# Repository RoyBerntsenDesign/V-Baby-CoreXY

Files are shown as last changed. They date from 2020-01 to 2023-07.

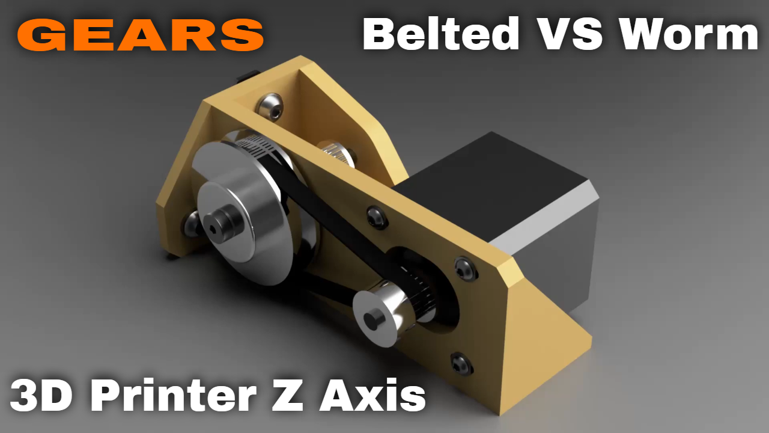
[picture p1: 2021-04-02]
Part Print Files/Stock Parts/Base Frame Parts/Z Gear Belted/Belted Gear 00.png

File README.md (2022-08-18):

# V-Baby CoreXY 3d Printer
The desktop CoreXY 3d Printer by Roy Berntsen - OpenSource - OpenBuilds Machine

In this repository you will find the print files, source files and documentation for the V-Baby 3D printer. If you are missing a part or information of feel free to file an issue on github

You can be a supporter of the develompent on patreon here: https://www.patreon.com/pro3d?fan_landing=true
Or if you want to buy me a coffe to keep the pace going in this project:

<a href="https://www.buymeacoffee.com/pro3d" target="_blank">Buy Me A Coffee</a>

Community links: https://www.facebook.com/vking3d/ - https://www.facebook.com/groups/viking3d/

All files are released according to the following license unless specified differently in the file or directory:
CC-by-NC: http://creativecommons.org/licenses/by-nc/3.0/

Roy Berntsen - Research and Development

3d model for view and download
V1 Top Assembly: https://a360.co/3PA3aYa

V-Baby 12 00

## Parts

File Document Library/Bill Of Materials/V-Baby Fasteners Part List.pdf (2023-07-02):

Part Name | Description | Quantity | Order Quantity
M2 NUT | Nut Standard | 2 | 2
M2,5 Nut | Nut Standard | 4 | 4
M2,5x16 BH | Low Profile Head | 4 | 4
M2x10 BH | Low Profile Head | 2 | 2
M3 Lock Nut | Nut Nylon Lock | 2 | 2
M3 Nut | Nut Standard | 11 | 11
M3 WASHER | Washer Standard | 15 | 15
M3x06 BH | Low Profile Head | 6 | 6
M3x08 BH | Low Profile Head | 9 | 9
M3x10 BH | Low Profile Head | 5 | 5
M3x12 BH | Low Profile Head | 8 | 8
M3x30 HEX | Hex Bolt | 2 | 2
M4 LOCK NUT | NUT Nylon LOCK | 5 | 5
M4 NUT | Nut Standard | 5 | 5
M4 WASHER | Washer Standard | 13 | 13
M4x10 BH | Low Profile Head | 6 | 6
M4x12 BH | Low Profile Head | 2 | 2
M4x16 BH | Low Profile Head | 1 | 1
M4x16 HEX | Hex Bolt | 3 | 3
M4x20 HEX | Hex Bolt | 1 | 1
M4x30 BH | Low Profile Head | 1 | 1
M5 LOCK NUT | NUT Nylon LOCK | 28 | 30
M5 Nut | Nut Standard | 6 | 6
M5 Nut Drop-In | Nut Drop In | 50 | 50
M5 Precision Shim 5X6X1 Precision Shim | 63 | 70
M5 T-Nut OB | OpenBuilds Tee Nut | 143 | 150
M5 WASHER | Washer Standard | 200 | 200
M5x10 BH | Low Profile Head | 142 | 150
M5x12 BH | Low Profile Head | 8 | 8
M5x16 BH | Low Profile Head | 1 | 1
M5x20 BH | Low Profile Head | 2 | 2
M5x25 BH | Low Profile Head | 2 | 2
M5x30 BH | Low Profile Head | 18 | 18
M5x35 BH | Low Profile Head | 8 | 8
M5x35 Bearing pin 5mm Bearing pin | 4 | 1x10
Number of fasteners | | 782 | 802
Approx Price/Pcs | | | $0.10
Approx Fasteners Price | $80.20

Part Name | Description

NB! See Component List

Quantity

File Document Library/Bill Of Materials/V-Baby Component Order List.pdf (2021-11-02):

V-Baby CoreXY Part (https://www.buymeacoffee.com/pro3d) List

MakerSupplies Mechanical Kit (https://makersupplies.dk/en/corexy-3d-printer/446-corexy-3d-printer-small-mechanical-kit-for-v-baby-corexy-3d-printer-200mm.html) <<-- ALL HARDWARE KIT HERE $334.00
Part Name | Description | Quantity | AliExpress Link | Price | Optional Component Price2
10mm Belt Idler Smooth | Smooth Idler for 10mm belt | 4 | Size: W 11mm without t (https://s.click.aliexpress.com/e/_AVt9fH) | $16.00
10mm Belt Idler Thoothed | Thoothed Idler for 10mm belt | 2 | Size: W 11mm with t (https://s.click.aliexpress.com/e/_AVt9fH) | $10.00
10mm Belt Z Gear Pulley | Pulley for the Belted Z Gear | 1 | Size: For 10mm 1 pcs (https://s.click.aliexpress.com/e/_Ae26J6) | $5.00
10mm Timing Belt | 2GT Timing Belt 10W 2 Meter | 4 meter | Size: 2M Color: 2GT 10MM (https://s.click.aliexpress.com/e/_A1bwlD) | $22.00
6mm Belt Idler Smooth | Smooth Idler for 6mm belt | 2 | Size: W 7mm without t (https://s.click.aliexpress.com/e/_AVt9fH) | $10.00
6mm Belt Idler Thoothed | Thoothed Idler for 6mm belt | 6 | Size: W 7mm with t (https://s.click.aliexpress.com/e/_AVt9fH) | $28.00
6mm Belt Motor Pulley | GT2 20T 6W 5mm Bore | 2 | Size: Bore 5 width 6 (https://s.click.aliexpress.com/e/_Aag7aB) | $11.00
6mm Timing Belt | 2GT Timing Belt 6W 4 Meter | 4 meter | Size: 4M-6MM-2GT (https://s.click.aliexpress.com/e/_A3kbnW) | $19.00
Belt Idler Bearing shafts | Bearing shafts 5mm | 1x6 | 5mm Length: 35mm 6PC (https://s.click.aliexpress.com/e/_A2xCLl) | $3.00
Belt Idler Precision Shim | 6.5x5x1 mm Precision Shim | 80 | Size: 6.5x5x1mm (https://www.aliexpress.com/item/32874190317.html) | $15.00
Bowden Tube | 1.9ID 4OD Filament Tube | 1 | Size: Black 1M (https://s.click.aliexpress.com/e/_A8XHCT) | $2.50
Cable Loom Tube | Tube for Hotend Cables | 1 | 20mmx1m Cable Loom (https://s.click.aliexpress.com/e/_dTFkJul) | $2.50
Cable Sleeve Nylon | Sleeve for Heatbed cables | 1 | 10 mm Sleeve (https://s.click.aliexpress.com/e/_dSOVNYp) | $8.00
Controller Board | Duet WIFI Clone w/TMC2660 | 1 | BTT DUET WIFI Clone (https://s.click.aliexpress.com/e/_AK6uHu) | $60.00
Extruder | BMG Type Filament Extruder | 1 | TriangleLab BMG (https://s.click.aliexpress.com/e/_AoiXQz) | $31.00
Fan for Cabinet cooling | 4010 Axial Fan 12/24V | 2 | Blade Color: 24V Ball (https://s.click.aliexpress.com/e/_9AUPbv) | $10.00
Fan for Hotend cooling | 4010 Blower Fan 12/24V | 1 | Blade Color: 24V Ball 9500RPM (https://s.click.aliexpress.com/e/_ATvGsB) | $2.00
Fan For Part Cooling | 3010 Blower Fan 5/12 24V | 2 | Blade Color: 24v dual ball (http://s.click.aliexpress.com/e/bele3ZZI) | $10.00
Heatbed Build Plate | Milled Cast Aluminum | 1 | 6mm 210x210 mm (https://makersupplies.dk/metal/816-metal-cnc-milled-cast-aluminum-plate.html) | $30.00 | Rolled Aluminum 5mm (http://s.click.aliexpress.com/e/bYQLqeBW) | $16.00
Hotend | Dragon Hotend | 1 | Dragonfly Phateus Color: BMO (https://s.click.aliexpress.com/e/_9z8pWX) | $73.00
Nema 17 1.8 A | Stepper motor 1.8 Amp | 1x5 | 5Pack & Cable (https://s.click.aliexpress.com/e/_AtomW3) | $30.00
Optical Endstops | XY(Z) Endstops | 1x6 | 6Pack Endstops (http://s.click.aliexpress.com/e/Im2VNR3) | $4.00
Power Switch | 10A 250VAC Fused Switch | 1 | 10A Fused Switch (http://s.click.aliexpress.com/e/blNcy7Lw) | $8.50
Powersupply | 24V 240W PSU | 1 | 24V 10A 240W (http://s.click.aliexpress.com/e/4GAsFeg) | $20.00
Safety Fuse | Thermal Safety Fuse for SSR | 1 | 135 Deg Fuse (http://s.click.aliexpress.com/e/bu7dz62U) | $2.00
Silicon Bed Heater | 200x200 110V/220V Heater | 1 | Kenoovo 240V 400W (https://s.click.aliexpress.com/e/_APr1gj) | $40.00
Solid State Relay | Silicone Heater Relay Switch | 1 | SSR 40DA (http://s.click.aliexpress.com/e/ckUQTj4c) | $3.50
Z 3:1 GT2 Gear | GT2 Pulleys and 200 mm Belt | 1 | Size: 20T5 - 60T5:Color: 200MM (https://s.click.aliexpress.com/e/_9QiZzH) | $8.50
Z Drive Gear Bearings | 625RS Bearings | 1x10 | 10Pcs 625RS (https://s.click.aliexpress.com/e/_9AmX7Z) | $19.00
Z Drive Gear Pulley Bolt | Bolt for the Gear Pulleys | 1 | Dia 5mm Length: 60mm (https://s.click.aliexpress.com/e/_A6tRQF) | $6.00
Z Leveling Probe | 3D Touch Leveling Probe | 1 | 3D Touch (http://s.click.aliexpress.com/e/bhxMAOUo) | $14.00
Component Total Price | | | | $523.50
Price inclusive mech kit | | | | USD 857.50

Research, Development & Design by:
Roy Berntsen M.Sc. Engineering Designer (https://www.buymeacoffee.com/pro3d)

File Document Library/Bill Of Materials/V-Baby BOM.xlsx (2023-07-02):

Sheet: OpenBuild Part List
Exstrusions | Part Name | Description | Quantity | Length mm | OpenBuilds Kit | AliExpress Parts |  | Price
 |  |  |  |  | Frame - Wheels - Brackets - Fasterners + Cutts & Tapping (https://makersupplies.dk/corexy-3d-printer/446-corexy-3d-printer-beta-version-base-mechanical-kit-for-baby-corexy-3d-printer.html)
X Direction | 2020 V-Slot X Axis | 310mm V-Slot | 4 | 1240
Y Direction | 2020 V-Slot Y Axis | 350mm V-Slot Tapped | 4 | 1400
Z Direction | 2020 V-Slot Z Axis | 340mm V-Slot | 5 | 1700
X Axis | 2020 V-Slot X Axis | 295mm V-Slot | 1 | 295
X Bed Frame | 2020 V-Slot Bed Frame X | 2020 V-Slot 290 | 1 | 290
Y Bed Frame | 2020 V-Slot Bed Frame Y | 2020 V-Slot 350 | 2 | 700 |  | No cuts - No tapps
Total | V-Slot | V-Slot in Meter |  | 5625 |  | 17x350 (https://s.click.aliexpress.com/e/_AVYFX8) | V-Slots | $21.00
 |  |  |  |  |  | Shipping |  | $108.00
Printer | V-Wheel Mini Assy | V-Wheel Mini Assy | 18 |  |  | 2 X 10 Pack (http://s.click.aliexpress.com/e/bnir7Lze) | Wheels | $15.00
Base Frame | 2820 L Bracket | Corner Bracket | 30 |  |  | 2 X 20 Pack (http://s.click.aliexpress.com/e/biEt0RTE) | Brackets | $14.00
OpenBuild Part Price |  |  |  |  | $360.00 |  |  | $158.00
OpenBuild Parts Price |  |  |  |  | $360.00 | AliExpress |  | $158.00
Component Part Price |  |  |  |  | $523.50 | Component Part Price |  | $523.50
Cable Management |  |  |  |  | - | Cable Management |  | -
Fasteners Part Price |  |  |  |  | Included | Fasteners Part Price |  | $80.20
Total Printer Price wo/Tax & Shipping |  |  |  |  | $883.50 | Total |  | $761.70

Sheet: V-Slot Calculator
V-Slot Calculator
V-Baby 200 |  | Pcs | V-Baby 250 |  | V-Baby 300
X Base Frame | 310 | x4 | 360 |  | 410
Y Base Frame | 350 | x4 | 400 | Tapped | 450 | Tapped
Z Base Frame | 340 | x5 | 390 |  | 440
X Bed Frame | 290 | x1 | 340 |  | 390
Y Bed Frame | 350 | x2 | 400 |  | 450
X Axis | 295 | x1 | 345 |  | 395
V-Baby XYZ
Configure Your Own
Add your wanted travel here: |  | mm | Needed Extrusion Length: |  | Pcs
X Base Frame | 390 | X | 500 |  | x4
Y Base Frame | 350 | Y | 500 |  | x4 | Tapped
Z Base Frame | 360 | Z | 500 |  | x5
X Bed Frame |  |  | 480 |  | x1
Y Bed Frame |  |  | 500 |  | x2
X Axis |  |  | 485 |  | x1
You Can Support the Development Here:
https://www.buymeacoffee.com/pro3d
https://www.patreon.com/pro3d

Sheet: Component Part List
 |  |  | V-Baby CoreXY Part List
MakerSupplies Mechanical Kit (https://makersupplies.dk/en/corexy-3d-printer/446-corexy-3d-printer-small-mechanical-kit-for-v-baby-corexy-3d-printer-200mm.html) |  | <<-- ALL HARDWARE KIT HERE |  | $334.00
Part Name | Description | Quantity | AliExpress Link | Price | Optional Component | Price2
10mm Belt Idler Smooth | Smooth Idler for 10mm belt | 4 | Size: W 11mm without t (https://s.click.aliexpress.com/e/_AVt9fH) | $16.00
10mm Belt Idler Thoothed | Thoothed Idler for 10mm belt | 2 | Size: W 11mm with t (https://s.click.aliexpress.com/e/_AVt9fH) | $10.00
10mm Belt Z Gear Pulley | Pulley for the Belted Z Gear | 1 | Size: For 10mm 1 pcs (https://s.click.aliexpress.com/e/_Ae26J6) | $5.00
10mm Timing Belt | 2GT Timing Belt 10W 2 Meter | 4 meter | Size: 2M Color: 2GT 10MM (https://s.click.aliexpress.com/e/_A1bwlD) | $22.00
6mm Belt Idler Smooth | Smooth Idler for 6mm belt | 2 | Size: W 7mm without t (https://s.click.aliexpress.com/e/_AVt9fH) | $10.00
6mm Belt Idler Thoothed | Thoothed Idler for 6mm belt | 6 | Size: W 7mm with t (https://s.click.aliexpress.com/e/_AVt9fH) | $28.00
6mm Belt Motor Pulley | GT2 20T 6W 5mm Bore | 2 | Size: Bore 5 width 6 (https://s.click.aliexpress.com/e/_Aag7aB) | $11.00
6mm Timing Belt | 2GT Timing Belt 6W 4 Meter | 4 meter | Size: 4M-6MM-2GT (https://s.click.aliexpress.com/e/_A3kbnW) | $19.00
Belt Idler Bearing shafts | Bearing shafts 5mm | 1x6 | 5mm Length: 35mm 6PC (https://s.click.aliexpress.com/e/_A2xCLl) | $3.00
Belt Idler Precision Shim | 6.5x5x1 mm Precision Shim | 80 | Size: 6.5x5x1mm (https://www.aliexpress.com/item/32874190317.html) | $15.00
Bowden Tube | 1.9ID 4OD Filament Tube | 1 | Size: Black 1M (https://s.click.aliexpress.com/e/_A8XHCT) | $2.50
Cable Loom Tube | Tube for Hotend Cables | 1 | 20mmx1m Cable Loom (https://s.click.aliexpress.com/e/_dTFkJul) | $2.50
Cable Sleeve Nylon | Sleeve for Heatbed cables | 1 | 10 mm Sleeve (https://s.click.aliexpress.com/e/_dSOVNYp) | $8.00
Controller Board | Duet WIFI Clone w/TMC2660 | 1 | BTT DUET WIFI Clone (https://s.click.aliexpress.com/e/_AK6uHu) | $60.00
Extruder | BMG Type Filament Extruder | 1 | TriangleLab BMG (https://s.click.aliexpress.com/e/_AoiXQz) | $31.00
Fan for Cabinet cooling | 4010 Axial Fan 12/24V | 2 | Blade Color: 24V Ball (https://s.click.aliexpress.com/e/_9AUPbv) | $10.00
Fan for Hotend cooling | 4010 Blower Fan 12/24V | 1 | Blade Color: 24V Ball 9500RPM (https://s.click.aliexpress.com/e/_ATvGsB) | $2.00
Fan For Part Cooling | 3010 Blower Fan 5/12 24V | 2 | Blade Color: 24v dual ball (http://s.click.aliexpress.com/e/bele3ZZI) | $10.00
Heatbed Build Plate | Milled Cast Aluminum | 1 | 6mm 210x210 mm (https://makersupplies.dk/metal/816-metal-cnc-milled-cast-aluminum-plate.html) | $30.00 | Rolled Aluminum 5mm (http://s.click.aliexpress.com/e/bYQLqeBW) | $16.00
Hotend | Dragon Hotend | 1 | Dragonfly Phateus Color: BMO (https://s.click.aliexpress.com/e/_9z8pWX) | $73.00
Nema 17 1.8 A | Stepper motor 1.8 Amp | 1x5 | 5Pack & Cable (https://s.click.aliexpress.com/e/_AtomW3) | $30.00
Optical Endstops | XY(Z) Endstops | 3 | 3PCS (https://s.click.aliexpress.com/e/_ASe8tS) | $4.00
Power Switch | 10A 250VAC Fused Switch | 1 | 10A Fused Switch (https://s.click.aliexpress.com/e/_AX4lXw) | $8.50
Powersupply | 24V 240W PSU | 1 | 24V 10A 240W (http://s.click.aliexpress.com/e/4GAsFeg) | $20.00
Safety Fuse | Thermal Safety Fuse for SSR | 1 | 135 Deg Fuse (http://s.click.aliexpress.com/e/bu7dz62U) | $2.00
Silicon Bed Heater | 200x200 110V/220V Heater | 1 | Kenoovo 240V 400W (https://s.click.aliexpress.com/e/_APr1gj) | $40.00
Solid State Relay | Silicone Heater Relay Switch | 1 | SSR 40DA (http://s.click.aliexpress.com/e/ckUQTj4c) | $3.50
Z 3:1 GT2 Gear | GT2 Pulleys and 200 mm Belt | 1 | Size: 20T5 - 60T5:Color: 200MM (https://s.click.aliexpress.com/e/_9QiZzH) | $8.50
Z Drive Gear Bearings | 625RS Bearings | 1x10 | 10Pcs 625RS (https://s.click.aliexpress.com/e/_9AmX7Z) | $19.00
Z Drive Gear Pulley Bolt | Bolt for the Gear Pulleys | 1 | Dia 5mm Length: 60mm (https://s.click.aliexpress.com/e/_A6tRQF) | $6.00
Z Leveling Probe | 3D Touch Leveling Probe | 1 | 3D Touch (http://s.click.aliexpress.com/e/bhxMAOUo) | $14.00
Component Total Price |  |  |  | $523.50
Price inclusive mech kit |  |  |  | USD 857.50

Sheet: Fasteners
Part Name | Description | Quantity | Order Quantity |  | Part Name | Description | Quantity
M2 NUT | Nut Standard | 2 | 2
M2,5 Nut | Nut Standard | 4 | 4
M2,5x16 BH | Low Profile Head | 4 | 4
M2x10 BH | Low Profile Head | 2 | 2
M3 Lock Nut | Nut Nylon Lock | 2 | 2
M3 Nut | Nut Standard | 11 | 11
M3 WASHER | Washer Standard | 15 | 15
M3x06 BH | Low Profile Head | 6 | 6
M3x08 BH | Low Profile Head | 9 | 9
M3x10 BH | Low Profile Head | 5 | 5
M3x12 BH | Low Profile Head | 8 | 8
M3x30 HEX | Hex Bolt | 2 | 2
M4 LOCK NUT | NUT Nylon LOCK | 5 | 5
M4 NUT | Nut Standard | 5 | 5
M4 WASHER | Washer Standard | 13 | 13
M4x10 BH | Low Profile Head | 6 | 6
M4x12 BH | Low Profile Head | 2 | 2
M4x16 BH | Low Profile Head | 1 | 1
M4x16 HEX | Hex Bolt | 3 | 3
M4x20 HEX | Hex Bolt | 1 | 1
M4x30 BH | Low Profile Head | 1 | 1
M5 LOCK NUT | NUT Nylon LOCK | 28 | 30
M5 Nut | Nut Standard | 6 | 6
M5 Nut Drop-In | Nut Drop In | 50 | 50
M5 Precision Shim | 5X6X1 Precision Shim | 63 | 70 | NB! See Component List
M5 T-Nut OB | OpenBuilds Tee Nut | 143 | 150
M5 WASHER | Washer Standard | 200 | 200
M5x10 BH | Low Profile Head | 142 | 150
M5x12 BH | Low Profile Head | 8 | 8
M5x16 BH | Low Profile Head | 1 | 1
M5x20 BH | Low Profile Head | 2 | 2
M5x25 BH | Low Profile Head | 2 | 2
M5x30 BH | Low Profile Head | 18 | 18
M5x35 BH | Low Profile Head | 8 | 8
M5x35 Bearing pin | 5mm Bearing pin (https://s.click.aliexpress.com/e/_DDzLeEd) | 4 | 1x10
Number of fasteners |  | 782 | 802
Approx Price/Pcs |  |  | $0.10
Approx Fasteners Price |  |  | $80.20

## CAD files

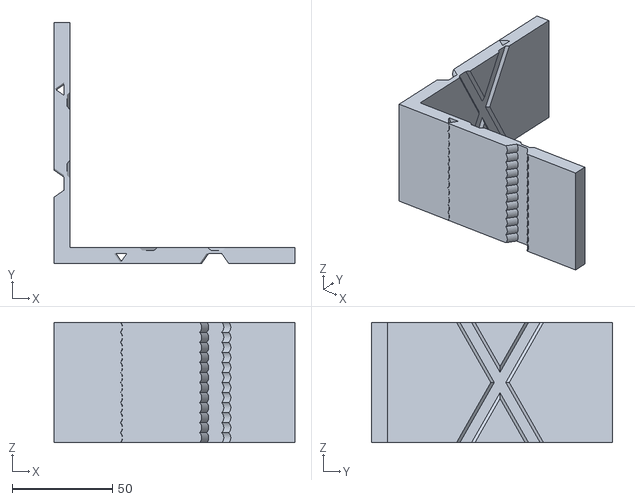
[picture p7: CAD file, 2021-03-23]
Part Print Files/Calibration Files/ringing_tower.stl
120.0 x 120.0 x 60.0

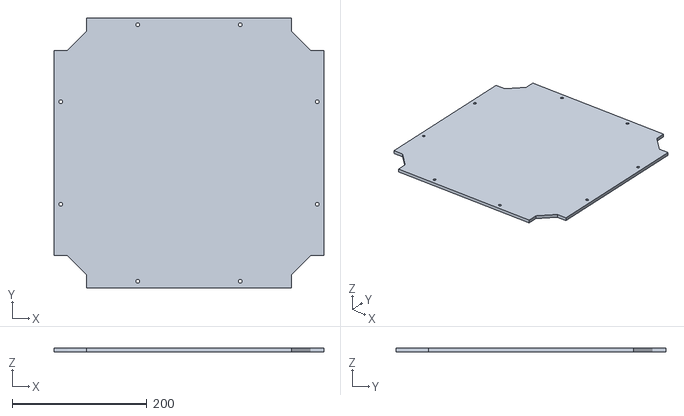
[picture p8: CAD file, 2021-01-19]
Part Print Files/Option Parts/250 Panels/250 Bottom Plate_1x.stl
400.0 x 400.0 x 6.00

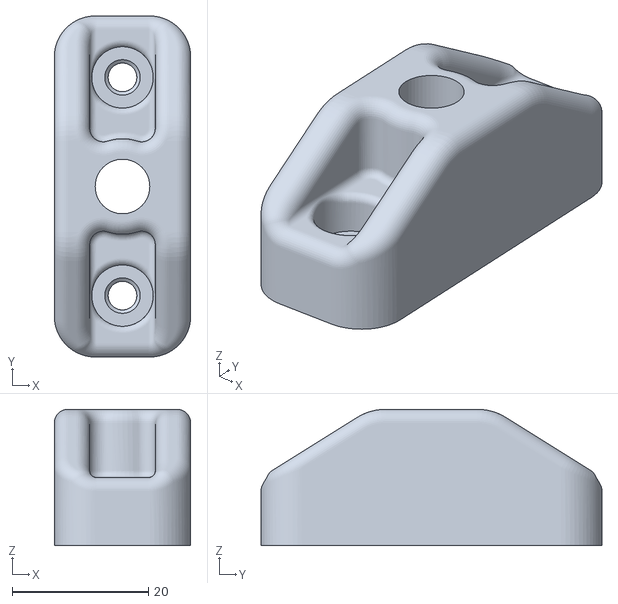
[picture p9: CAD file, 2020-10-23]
Part Print Files/Option Parts/Bearing Spool Holder/Spool Holder Base 1x_SN_BN_100%.stl
20.0 x 50.0 x 20.0

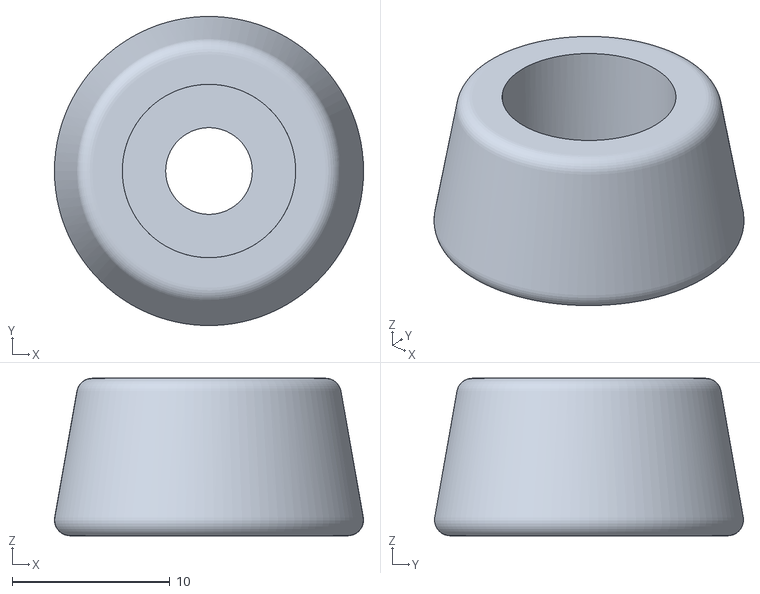
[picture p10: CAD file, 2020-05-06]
Part Print Files/Option Parts/Leg Parts/Leg TPU Bumper.stl
19.6 x 19.6 x 10.00

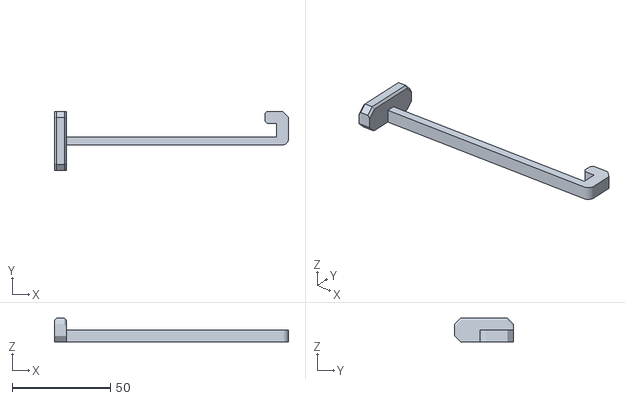
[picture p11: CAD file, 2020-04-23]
Part Print Files/Option Parts/Tools Parts/Bed Frame Hook B1_1x_SN_BN.stl
119.0 x 30.0 x 12.0

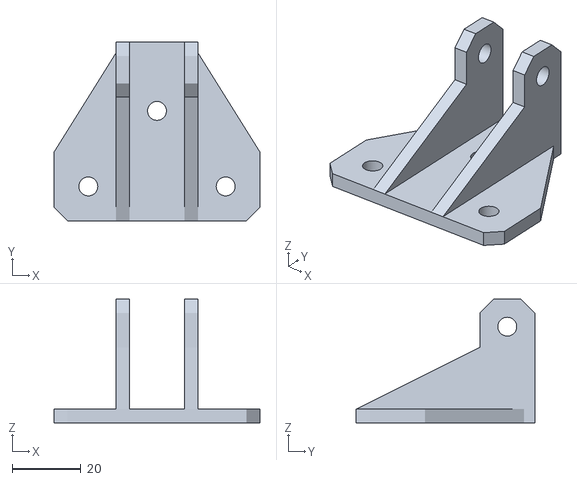
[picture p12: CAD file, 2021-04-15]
Part Print Files/Stock Parts/Base Frame Parts/10mm Z Belt Top Rear Idler Buddy_1x_SN_BN.stl
60.0 x 52.0 x 36.0

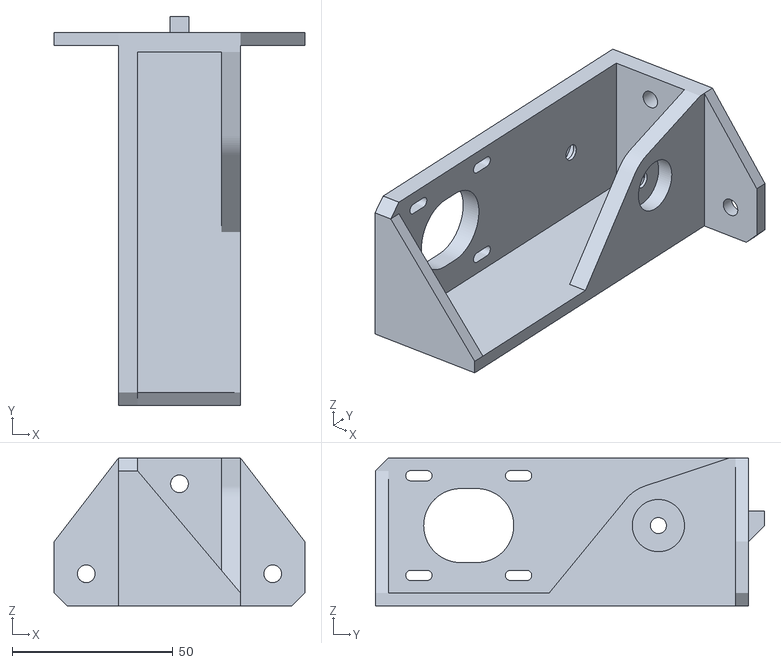
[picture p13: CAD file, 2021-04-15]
Part Print Files/Stock Parts/Base Frame Parts/Z Gear Belted/Z Belted Gear Buddy_SN.stl
78.0 x 121.0 x 46.0

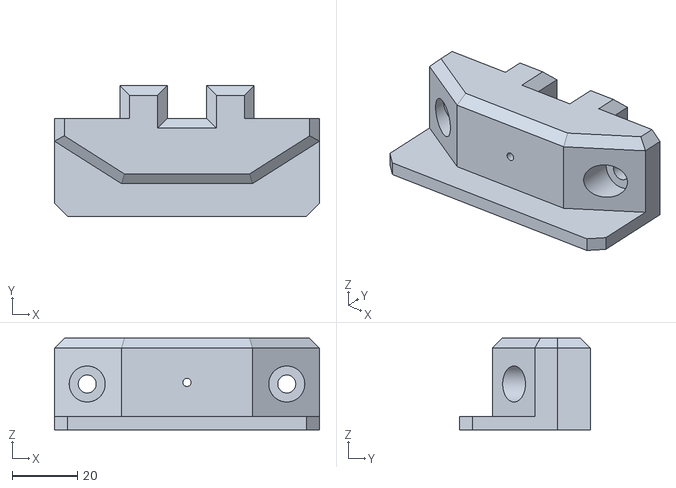
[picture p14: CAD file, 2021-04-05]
Part Print Files/Stock Parts/Bed Frame Parts/Bed Support Center_1x_SN_BN.stl
81.0 x 40.0 x 28.0

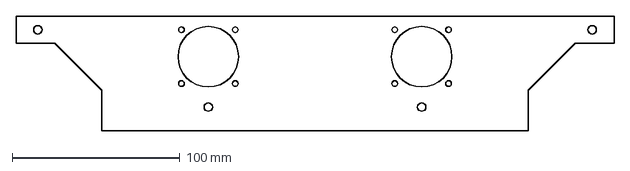
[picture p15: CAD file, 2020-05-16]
Part Print Files/Stock Parts/Electronic Cabinet Parts/200 Panels/Panel Cut Pattern/Panel Rear Cut_1x.dxf
356.0 x 68.0 mm

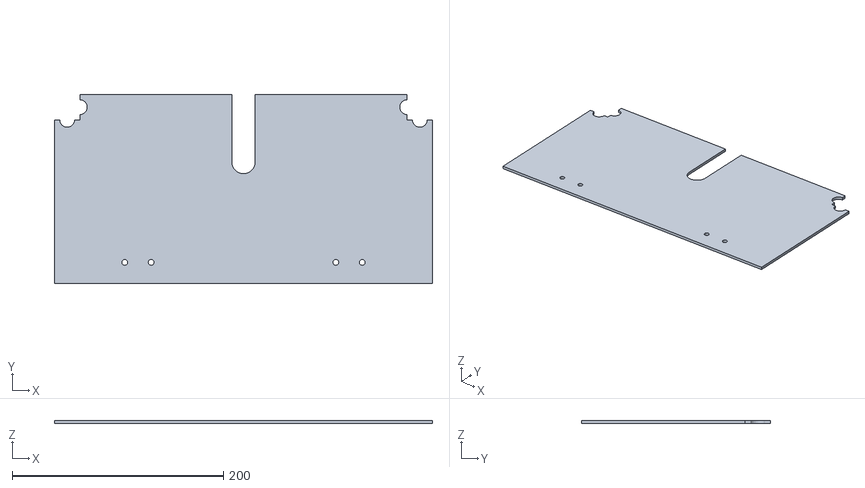
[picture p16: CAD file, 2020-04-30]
Part Print Files/Stock Parts/Electronic Cabinet Parts/200 Panels/Panel Top_B_1x_SN_BN_100%.stl
358.0 x 179.0 x 3.00

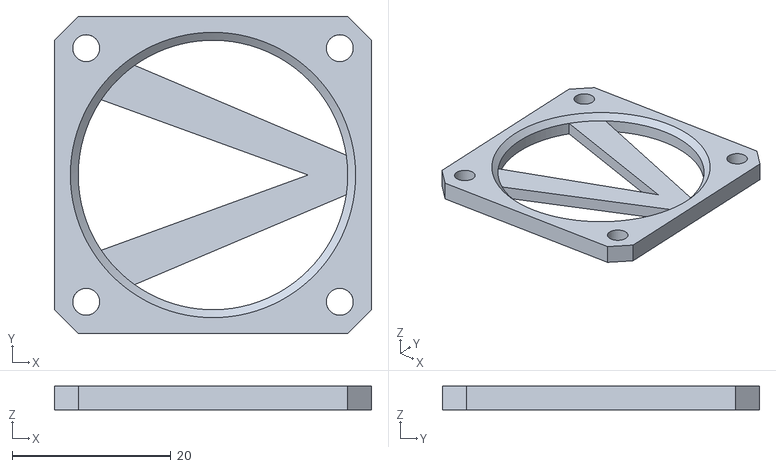
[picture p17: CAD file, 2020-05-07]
Part Print Files/Stock Parts/Electronic Cabinet Parts/4010 Fan Cover_2x.stl
40.0 x 40.0 x 3.00

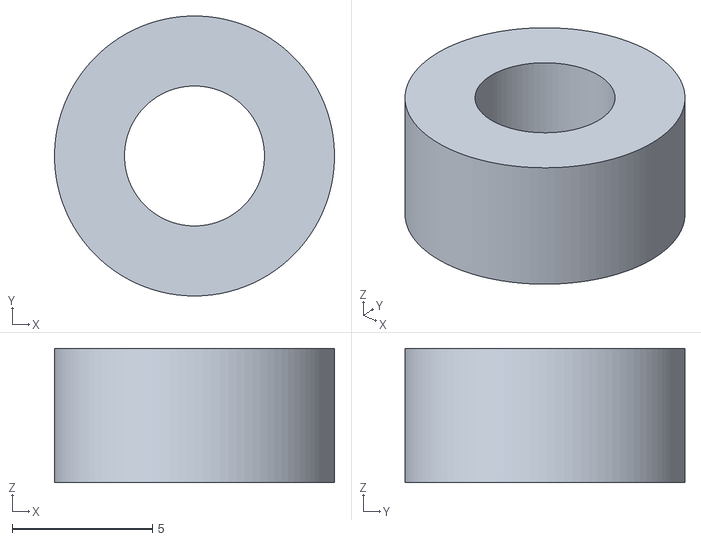
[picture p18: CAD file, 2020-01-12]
Part Print Files/Stock Parts/Fork Spacer_8x_SN_BO.stl
10.00 x 10.00 x 4.80

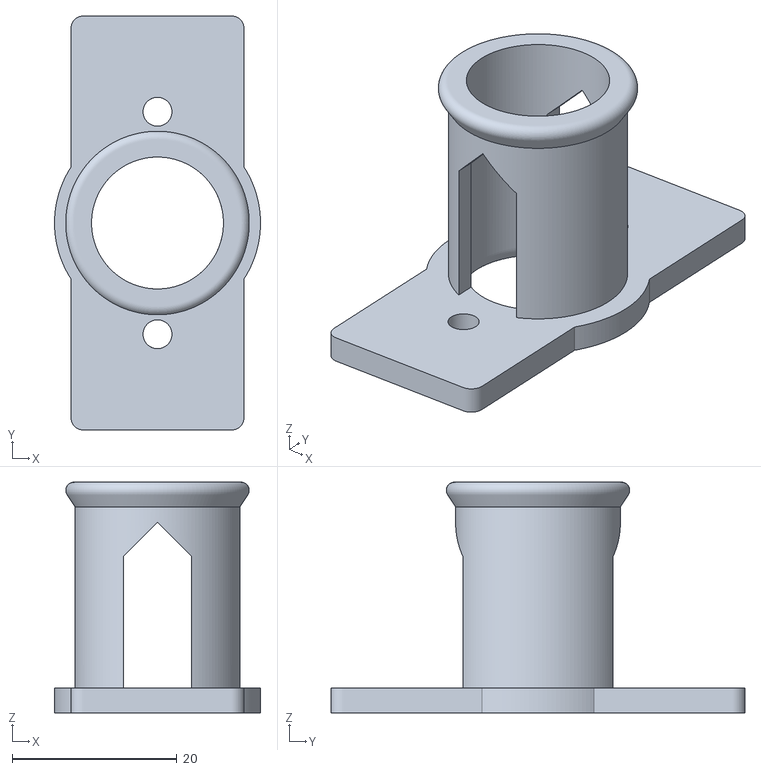
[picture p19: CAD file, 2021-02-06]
Part Print Files/Stock Parts/X Axis Parts/X Carrier Parts/Cable Loom Buddy_1x_SN_BN.stl
25.0 x 50.2 x 28.0

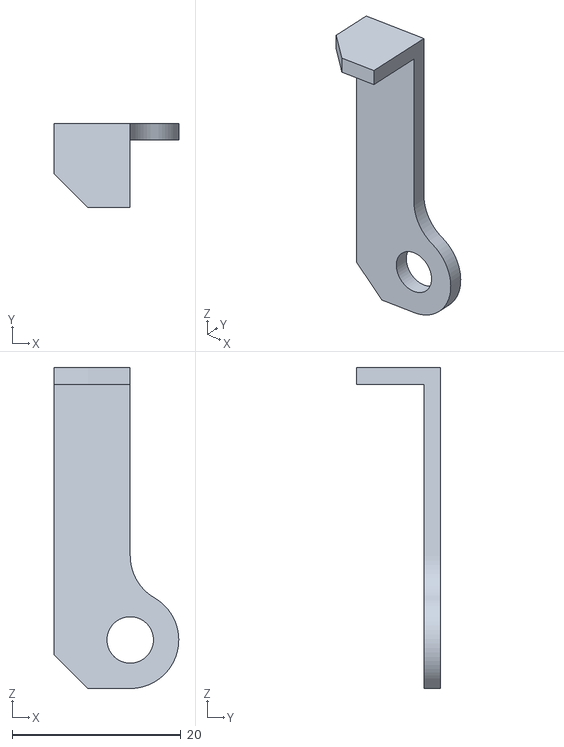
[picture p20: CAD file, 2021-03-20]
Part Print Files/Stock Parts/X Axis Parts/X Endstop Flag_1x_SN_BN.stl
14.7 x 10.0 x 38.0

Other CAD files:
Source Files/Panel Cut File Library/200/Panel Top-Front_Cut Pattern_1x.dxf
Source Files/Panel Cut File Library/250/250 Panel Bottom_Cut Pattern_1x.dxf
Source Files/Panel Cut File Library/300/300 Panel Side B_Cut Pattern_1x.dxf
Part Print Files/Calibration Files/Voron_Design_Cube_v7.stl
Part Print Files/Calibration Files/303020 Calibration Cube.stl
Part Print Files/Calibration Files/Stringing_Test.stl
Part Print Files/Calibration Files/xyzCalibration_cube.stl
Part Print Files/Calibration Files/z-wobble-test-square.stl
Part Print Files/Calibration Files/z-wobble-test.stl
Part Print Files/Electronic Cabinet Parts/Panels/Panel Bottom Cut_1x.dxf
Part Print Files/Electronic Cabinet Parts/Panels/Panel Rear Cut_1x.dxf
Part Print Files/Electronic Cabinet Parts/Panels/Panel Side A Cut_1x.dxf
Part Print Files/Electronic Cabinet Parts/Panels/Panel Side B Cut_1x.dxf
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

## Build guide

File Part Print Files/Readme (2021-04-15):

Slicer Recomendations
Material: PETG or similar as is more durable than PLA

Walls:      2 mm Shell
Bottom/Top: 2 mm shell
Layer Height: (Anything adding up in 1mm)
0.20
0.25
Infill: 20-25%

You do need a good calibrated extruder as parts are tight so check your flow
All parts are modeled with tolerance to fit

Suffix Explanation:
Example
- Filename_1x_SN_BN = 1x of this part, Support NO, Brim NO
- Filename_2x_SA_BY_30 = 2x of this part, Support ALL, Brim YES
- Filename_3x_SB_BO_50 = 3x of this part, Support BUILDPLATE, Brim OPTIONAL

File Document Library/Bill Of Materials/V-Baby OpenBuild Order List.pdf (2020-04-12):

Exstrusions | Part Name | Description | Quantity Length mm | OpenBuilds Kit | AliExpress Parts | Price
X Direction | 2020 V-Slot X Axis | 310mm V-Slot | 4 | 1240
Y Direction | 2020 V-Slot Y Axis | 350mm V-Slot Tapped | 4 | 1400
Z Direction | 2020 V-Slot Z Axis | 340mm V-Slot | 5 | 1700
X Axis | 2020 V-Slot X Axis | 295mm V-Slot | 1 | 295
X Bed Frame | 2020 V-Slot Bed Frame X | 2020 V-Slot 290 | 1 | 290
Y Bed Frame | 2020 V-Slot Bed Frame Y | 2020 V-Slot 350 | 2 | 700
Total | V-Slot | V-Slot in Meter | 5625 | 6 X 1000 mm (http://s.click.aliexpress.com/e/beClwsfA) | V-Slots | $27,00
Shipping | $50,00
Printer | V-Wheel Mini Assy | V-Wheel Mini Assy | 18 | 2 X 10 Pack (http://s.click.aliexpress.com/e/bnir7Lze) | Wheels | $15,00
Base Frame | 2820 L Bracket | Corner Bracket | 30 | 2 X 20 Pack (http://s.click.aliexpress.com/e/biEt0RTE) | Brackets | $12,00
OpenBuild Part Price | $314,00 | $104,00
OpenBuild Parts Price | $314,00 | AliExpress | $104,00
Component Part Price | 366,5 | Component Part Price | 366,5
Cable Management | - | Cable Management | -
Fasteners Part Price | Included | Fasteners Part Price | 80,6
Total Printer Price wo/Tax & Shipping | $680,50 | Total | $551,10

Frame -
Wheels -
Brackets -
Fasterners +
Cutts &
Tapping (https://makersupplies.dk/corexy-3d-printer/446-corexy-3d-printer-beta-version-base-mechanical-kit-for-baby-corexy-3d-printer.html)

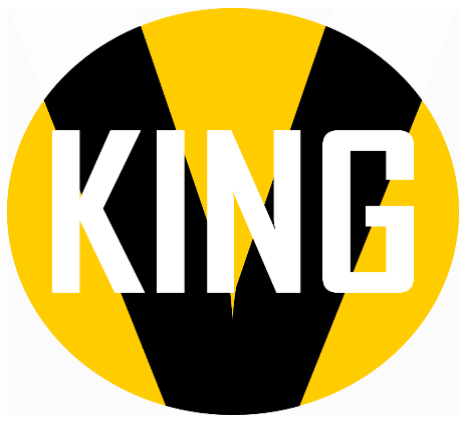
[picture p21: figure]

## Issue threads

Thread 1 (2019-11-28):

Link for Bottom Enclosure

tvixen, 2019-11-28:
Hi Roy
The link to Autodesk360 for Bottom Enclosure: https://a360.co/2GyqG7i
is not working.

Br Tim

tvixen, 2020-02-26:
Link is working again.

Closed 2020-02-26.

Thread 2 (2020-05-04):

Y Carrier Fork_2x_SN_BO protrusions prevent insertion into Y Carrier_2x_SB_BN

karllane, 2020-05-04:
There are protrusions at the end of the Y Carrier Fork that prevent it from being inserted into the Y Carrier.

RoyBerntsenDesign, 2020-05-04:
Oh right.. Thanks for mentioning. Let me fix that tonight

man. 4. mai 2020, 20:04 skrev karllane <notifications@github.com>:

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

RoyBerntsenDesign, 2020-10-23:
Resolved?

Closed 2020-10-23.

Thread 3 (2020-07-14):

Panel back cut pattern missing

gpupo, 2020-07-14:
Hi!
The back of the cabinet is missing in this repository, isn't it?

gpupo, 2020-07-15:
i was looking at ``Source Files`` but the right place to look is [Part%20Print%20Files/Stock%20Parts/Electronic%20Cabinet%20Parts/Panels/](https://github.com/RoyBerntsenDesign/V-Baby-CoreXY/tree/master/Part%20Print%20Files/Stock%20Parts/Electronic%20Cabinet%20Parts/Panels/Panel%20Cut%20Pattern)

Closed 2020-07-15.

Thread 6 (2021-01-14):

Using 12v system instead of 24

welo78, 2021-01-14:
Hello, first of all thank you for this wonderful project.

Second, I am in the midst of moving from HyperCube to either HevORT or your design. However since my hypercube uses parts of my old Anet A8, like 12v heatbed and the upgrades I bought for it (BMG, e3d V6 12v, fans, board) is it possible to use them ?

My build would be that much more cost efficent by not having to buy a 24v supply and so on. However idk if the TMC2209 work well with a 12v system.

Thanks for any advice.

RoyBerntsenDesign, 2021-01-14:
Welcome to the club and good luck with your choice of build.

You can use your current components on the V-Baby yes. 12Volt might need
some thicker cables as it creates much more amp than 24 volt so keep this
in mind when doing cable management.
 Also your current bed  is probably a thin sheet of aluminum waiting to
warp but this you probably are aware of from the Anet

I have some info on cable management on the wiki:
https://vkingprinter.com/knowledge-base/category/general3d/wiring/

Best regards/Vennlig hilsen
Roy Berntsen
M.Sc. Design Engineer
Tel: +47 928 26 012
E-mail: roy@pro3d.no
Web: www.pro3d.no

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

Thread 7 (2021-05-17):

Incorrectly named parts in the fusion360 model

ep1cman, 2021-05-17:
Some of the frame extrusions and the brearing shafts have incorrect lengths in their part names. E.g the 35mm bearing shafts are named `5x30 Bearing Shaft`. I now have 30 30mm shafts that i can't use.

I would suggest for parts like those to not include the dimensions in the file names if they are subject to change. I guess this wont work for screws but those shouldn't be an issue if they are all modeled correctly.

RoyBerntsenDesign, 2021-05-22:
Thank you for letting me know about this. You should be able to use the 30
one. The 35 extends out of what they need to.

man. 17. mai 2021, 19:57 skrev Sebastian Goscik ***@***.***>:

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

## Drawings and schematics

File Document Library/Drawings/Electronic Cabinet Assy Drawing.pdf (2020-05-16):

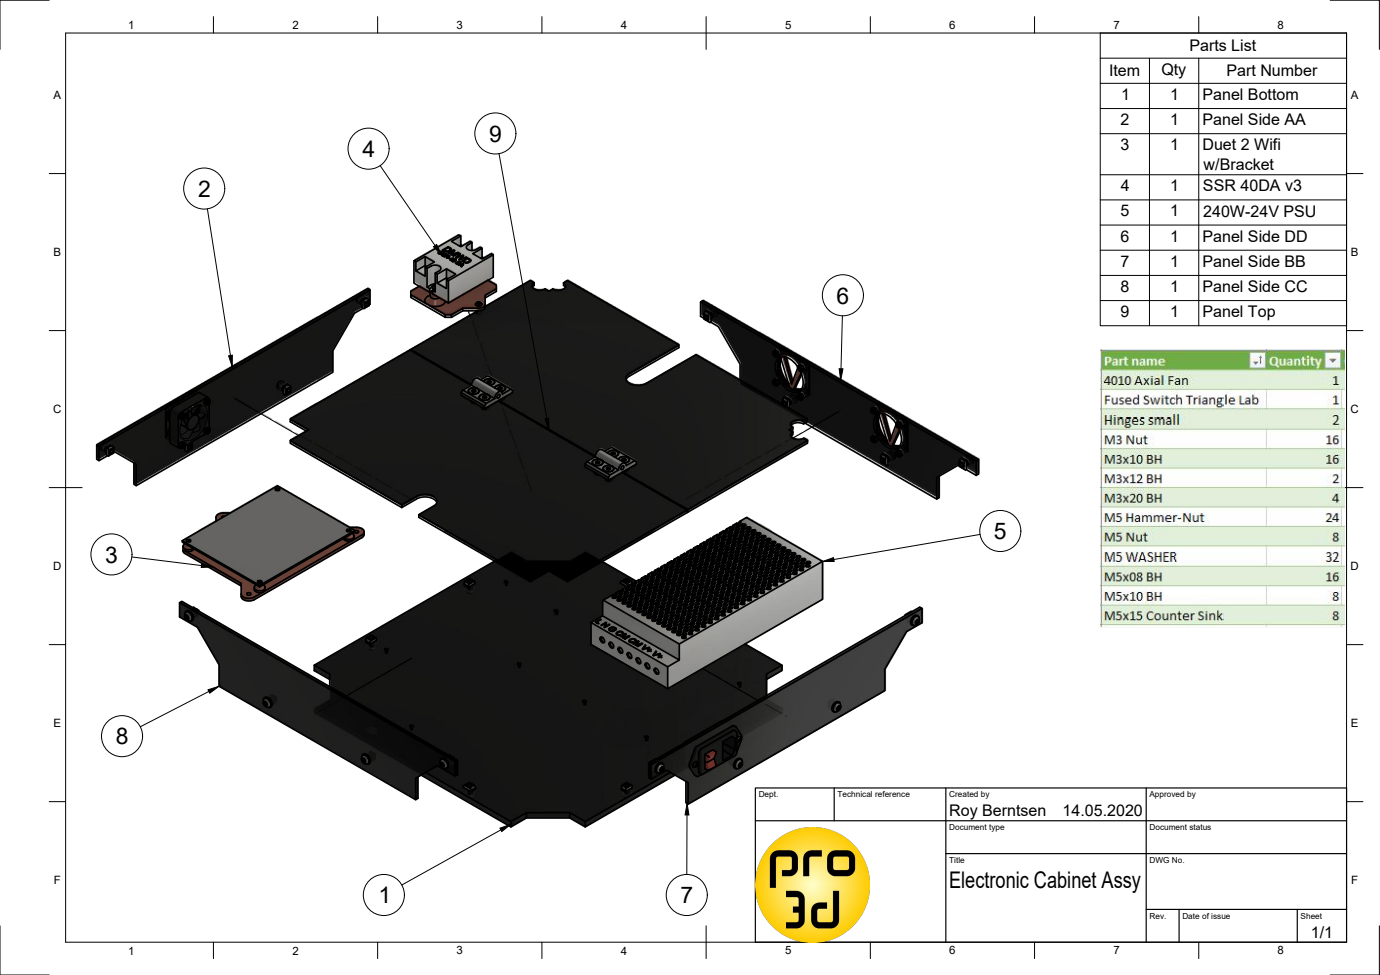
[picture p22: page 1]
Parts List

Item | Qty | Part Number
1 | 1 | Panel Bottom
2 | 1 | Panel Side AA
3 | 1 | Duet 2 Wifi w/Bracket

4 | 1 | SSR 40DA v3
5 | 1 | 240W-24V PSU
6 | 1 | Panel Side DD
7 | 1 | Panel Side BB
8 | 1 | Panel Side CC
9 | 1 | Panel Top

Dept. | Technical reference | Created by Roy Berntsen 14.05.2020 | Approved by

Document type | Document status

Title Electronic Cabinet Assy | DWG No.

Rev. | Date of issue | Sheet 1/1

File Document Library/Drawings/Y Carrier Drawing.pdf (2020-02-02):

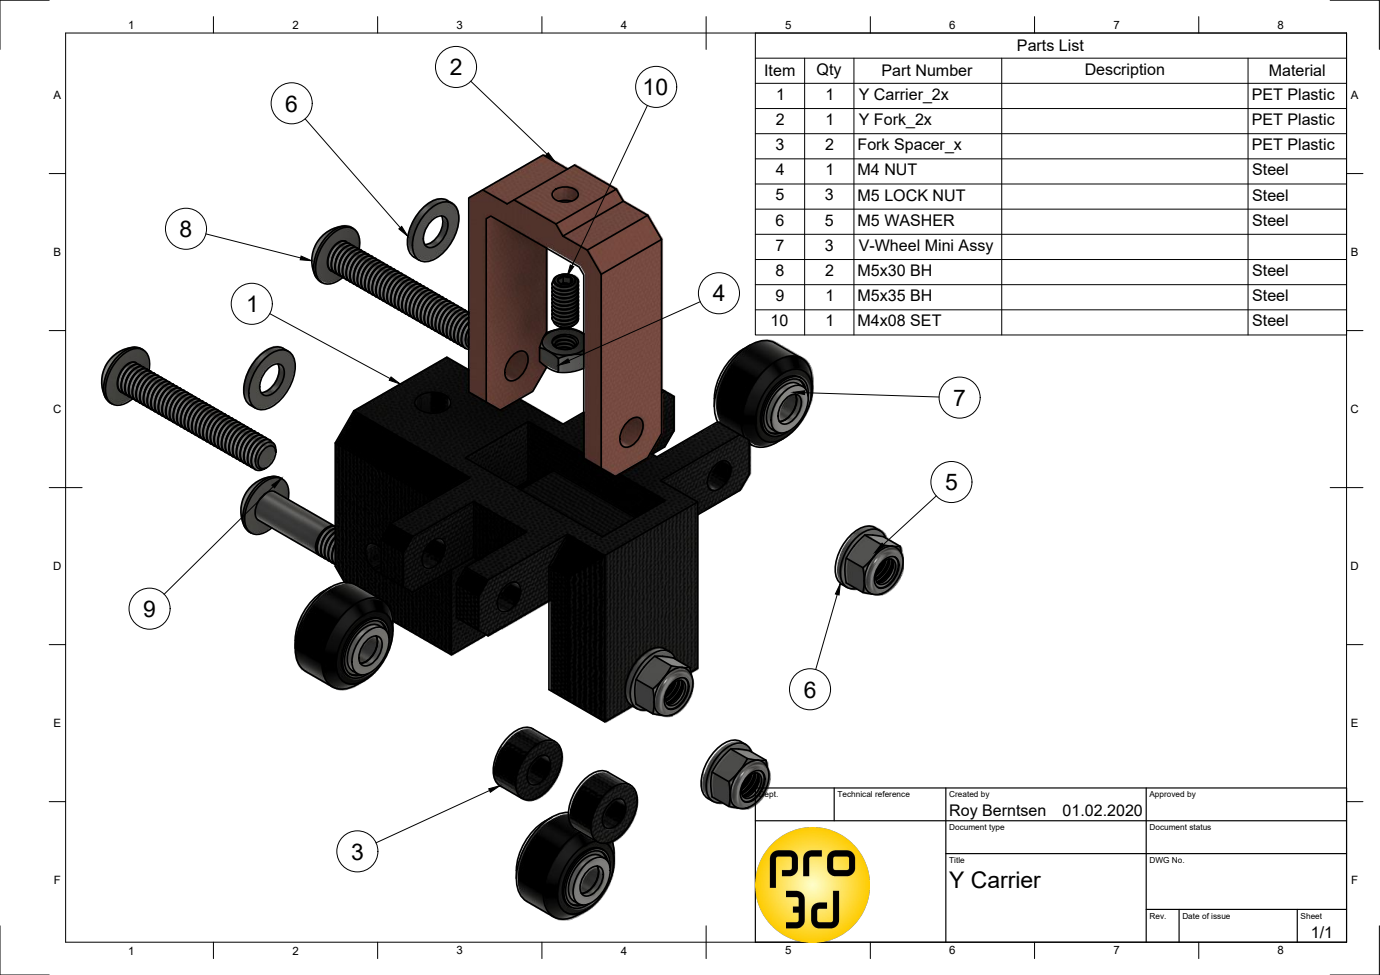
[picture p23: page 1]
Parts List

Item | Qty | Part Number | Description | Material
1 | 1 | Y Carrier_2x | | PET Plastic
2 | 1 | Y Fork_2x | | PET Plastic
3 | 2 | Fork Spacer_x | | PET Plastic
4 | 1 | M4 NUT | | Steel
5 | 3 | M5 LOCK NUT | | Steel
6 | 5 | M5 WASHER | | Steel
7 | 3 | V-Wheel Mini Assy
8 | 2 | M5x30 BH | | Steel
9 | 1 | M5x35 BH | | Steel
10 | 1 | M4x08 SET | | Steel

Dept. | Technical reference | Created by Roy Berntsen 01.02.2020 | Approved by

Document type | Document status

Title Y Carrier | DWG No.

Rev. | Date of issue | Sheet 1/1

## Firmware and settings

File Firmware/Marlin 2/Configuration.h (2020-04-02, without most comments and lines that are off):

#pragma once
#define CONFIGURATION_H_VERSION 020000
#define STRING_CONFIG_H_AUTHOR "(none, default config)" // Who made the changes.
#define SHOW_BOOTSCREEN
#define SERIAL_PORT -1
#define BAUDRATE 250000
  #define MOTHERBOARD BOARD_BIGTREE_SKR_V1_3
#define CUSTOM_MACHINE_NAME "V-Baby CXY"
#define EXTRUDERS 1
#define DEFAULT_NOMINAL_FILAMENT_DIA 1.75
#define TEMP_SENSOR_0 5
#define TEMP_SENSOR_1 0
#define TEMP_SENSOR_2 0
#define TEMP_SENSOR_3 0
#define TEMP_SENSOR_4 0
#define TEMP_SENSOR_5 0
#define TEMP_SENSOR_BED 11
#define TEMP_SENSOR_CHAMBER 0
#define DUMMY_THERMISTOR_998_VALUE 25
#define DUMMY_THERMISTOR_999_VALUE 100
#define MAX_REDUNDANT_TEMP_SENSOR_DIFF 10
#define TEMP_RESIDENCY_TIME     10  // (seconds) Time to wait for hotend to "settle" in M109
#define TEMP_WINDOW              1  // (°C) Temperature proximity for the "temperature reached" timer
#define TEMP_HYSTERESIS          3  // (°C) Temperature proximity considered "close enough" to the target
#define TEMP_BED_RESIDENCY_TIME 10  // (seconds) Time to wait for bed to "settle" in M190
#define TEMP_BED_WINDOW          1  // (°C) Temperature proximity for the "temperature reached" timer
#define TEMP_BED_HYSTERESIS      3  // (°C) Temperature proximity considered "close enough" to the target
#define HEATER_0_MINTEMP   5
#define HEATER_1_MINTEMP   5
#define HEATER_2_MINTEMP   5
#define HEATER_3_MINTEMP   5
#define HEATER_4_MINTEMP   5
#define HEATER_5_MINTEMP   5
#define BED_MINTEMP        5
#define HEATER_0_MAXTEMP 275
#define HEATER_1_MAXTEMP 275
#define HEATER_2_MAXTEMP 275
#define HEATER_3_MAXTEMP 275
#define HEATER_4_MAXTEMP 275
#define HEATER_5_MAXTEMP 275
#define BED_MAXTEMP      150
#define PIDTEMP
#define BANG_MAX 255     // Limits current to nozzle while in bang-bang mode; 255=full current
#define PID_MAX BANG_MAX // Limits current to nozzle while PID is active (see PID_FUNCTIONAL_RANGE below); 255=full current
#define PID_K1 0.95      // Smoothing factor within any PID loop
  #define PID_FUNCTIONAL_RANGE 10 // If the temperature difference between the target temperature and the actual temperature
  #define DEFAULT_Kp 13
  #define DEFAULT_Ki 0.65
  #define DEFAULT_Kd 60
#define PIDTEMPBED
#define MAX_BED_POWER 255 // limits duty cycle to bed; 255=full current
  #define DEFAULT_bedKp 10.00
  #define DEFAULT_bedKi 3
  #define DEFAULT_bedKd 145
#define PREVENT_COLD_EXTRUSION
#define EXTRUDE_MINTEMP 170
#define PREVENT_LENGTHY_EXTRUDE
#define EXTRUDE_MAXLENGTH 1000
#define THERMAL_PROTECTION_HOTENDS // Enable thermal protection for all extruders
#define THERMAL_PROTECTION_BED     // Enable thermal protection for the heated bed
#define THERMAL_PROTECTION_CHAMBER // Enable thermal protection for the heated chamber
#define COREXY
#define USE_XMIN_PLUG
#define USE_YMIN_PLUG
#define USE_ZMIN_PLUG
#define ENDSTOPPULLUPS
#define X_MIN_ENDSTOP_INVERTING false // Set to true to invert the logic of the endstop.
#define Y_MIN_ENDSTOP_INVERTING false // Set to true to invert the logic of the endstop.
#define Z_MIN_ENDSTOP_INVERTING false // Set to true to invert the logic of the endstop.
#define X_MAX_ENDSTOP_INVERTING false // Set to true to invert the logic of the endstop.
#define Y_MAX_ENDSTOP_INVERTING false // Set to true to invert the logic of the endstop.
#define Z_MAX_ENDSTOP_INVERTING false // Set to true to invert the logic of the endstop.
#define Z_MIN_PROBE_ENDSTOP_INVERTING false // Set to true to invert the logic of the probe.
#define X_DRIVER_TYPE  TMC2209
#define Y_DRIVER_TYPE  TMC2209
#define Z_DRIVER_TYPE  TMC2208
#define E0_DRIVER_TYPE TMC2208
#define DEFAULT_AXIS_STEPS_PER_UNIT   { 80, 80, 4960, 406 }		//For 30:1 Z drive (it is 31:1 but says 30:1) - use 2756 for the 17:1
#define DEFAULT_MAX_FEEDRATE          { 300, 300, 5, 100 }
#define DEFAULT_MAX_ACCELERATION      { 3000, 3000, 100, 10000 }
#define DEFAULT_ACCELERATION          2000    // X, Y, Z and E acceleration for printing moves
#define DEFAULT_RETRACT_ACCELERATION  2000    // E acceleration for retracts
#define DEFAULT_TRAVEL_ACCELERATION   2000    // X, Y, Z acceleration for travel (non printing) moves
#define DEFAULT_EJERK   15.0  // May be used by Linear Advance
  #define JUNCTION_DEVIATION_MM 0.045 // (mm) Distance from real junction edge
#define S_CURVE_ACCELERATION
#define Z_MIN_PROBE_USES_Z_MIN_ENDSTOP_PIN
#define BLTOUCH
#define NOZZLE_TO_PROBE_OFFSET { 18, -18, -2 }
#define MIN_PROBE_EDGE 10
#define XY_PROBE_SPEED 8000
#define Z_PROBE_SPEED_FAST HOMING_FEEDRATE_Z
#define Z_PROBE_SPEED_SLOW (Z_PROBE_SPEED_FAST / 2)
#define Z_CLEARANCE_DEPLOY_PROBE   10 // Z Clearance for Deploy/Stow
#define Z_CLEARANCE_BETWEEN_PROBES  5 // Z Clearance between probe points
#define Z_CLEARANCE_MULTI_PROBE     5 // Z Clearance between multiple probes
#define Z_PROBE_LOW_POINT          -2 // Farthest distance below the trigger-point to go before stopping
#define Z_PROBE_OFFSET_RANGE_MIN -20
#define Z_PROBE_OFFSET_RANGE_MAX 20
#define Z_MIN_PROBE_REPEATABILITY_TEST
#define PROBING_FANS_OFF          // Turn fans off when probing
#define X_ENABLE_ON 0
#define Y_ENABLE_ON 0
#define Z_ENABLE_ON 0
#define E_ENABLE_ON 0 // For all extruders
#define DISABLE_X false
#define DISABLE_Y false
#define DISABLE_Z false
#define DISABLE_E false             // For all extruders
#define DISABLE_INACTIVE_EXTRUDER   // Keep only the active extruder enabled
#define INVERT_X_DIR false
#define INVERT_Y_DIR false
#define INVERT_Z_DIR true
#define INVERT_E0_DIR false
#define INVERT_E1_DIR false
#define INVERT_E2_DIR false
#define INVERT_E3_DIR false
#define INVERT_E4_DIR false
#define INVERT_E5_DIR false
#define X_HOME_DIR -1
#define Y_HOME_DIR -1
#define Z_HOME_DIR -1
#define X_BED_SIZE 200
#define Y_BED_SIZE 200
#define X_MIN_POS 0
#define Y_MIN_POS 0
#define Z_MIN_POS 0
#define X_MAX_POS X_BED_SIZE
#define Y_MAX_POS Y_BED_SIZE
#define Z_MAX_POS 200
#define MIN_SOFTWARE_ENDSTOPS
  #define MIN_SOFTWARE_ENDSTOP_X
  #define MIN_SOFTWARE_ENDSTOP_Y
#define MAX_SOFTWARE_ENDSTOPS
  #define MAX_SOFTWARE_ENDSTOP_X
  #define MAX_SOFTWARE_ENDSTOP_Y
  #define MAX_SOFTWARE_ENDSTOP_Z
#define FILAMENT_RUNOUT_SENSOR
  #define NUM_RUNOUT_SENSORS   1     // Number of sensors, up to one per extruder. Define a FIL_RUNOUT#_PIN for each.
  #define FIL_RUNOUT_INVERTING false // Set to true to invert the logic of the sensor.
  #define FIL_RUNOUT_PULLUP          // Use internal pullup for filament runout pins.
  #define FILAMENT_RUNOUT_SCRIPT "M600"
#define AUTO_BED_LEVELING_3POINT
#define LCD_BED_LEVELING
  #define MESH_EDIT_Z_STEP  0.025 // (mm) Step size while manually probing Z axis.
  #define LCD_PROBE_Z_RANGE 4     // (mm) Z Range centered on Z_MIN_POS for LCD Z adjustment
#define LEVEL_BED_CORNERS
  #define LEVEL_CORNERS_INSET 25    // (mm) An inset for corner leveling
  #define LEVEL_CORNERS_Z_HOP  4.0  // (mm) Move nozzle up before moving between corners
  #define LEVEL_CORNERS_HEIGHT 0.0  // (mm) Z height of nozzle at leveling points
#define Z_SAFE_HOMING
  #define Z_SAFE_HOMING_X_POINT ((X_BED_SIZE) / 2)    // X point for Z homing when homing all axes (G28).
  #define Z_SAFE_HOMING_Y_POINT ((Y_BED_SIZE) / 2)    // Y point for Z homing when homing all axes (G28).
#define HOMING_FEEDRATE_XY (60*60)
#define HOMING_FEEDRATE_Z  (4*60)
#define VALIDATE_HOMING_ENDSTOPS
#define EEPROM_SETTINGS     // Persistent storage with M500 and M501
#define EEPROM_CHITCHAT       // Give feedback on EEPROM commands. Disable to save PROGMEM.
#define HOST_KEEPALIVE_FEATURE        // Disable this if your host doesn't like keepalive messages
#define DEFAULT_KEEPALIVE_INTERVAL 2  // Number of seconds between "busy" messages. Set with M113.
#define BUSY_WHILE_HEATING            // Some hosts require "busy" messages even during heating
#define PREHEAT_1_LABEL       "PLA"
#define PREHEAT_1_TEMP_HOTEND 200
#define PREHEAT_1_TEMP_BED     70
#define PREHEAT_1_FAN_SPEED     0 // Value from 0 to 255
#define PREHEAT_2_LABEL       "PETG"
#define PREHEAT_2_TEMP_HOTEND 240
#define PREHEAT_2_TEMP_BED    80
#define PREHEAT_2_FAN_SPEED     0 // Value from 0 to 255
#define NOZZLE_PARK_FEATURE
  #define NOZZLE_PARK_POINT { (X_MIN_POS + 10), (Y_MAX_POS - 10), 20 }
  #define NOZZLE_PARK_XY_FEEDRATE 100   // (mm/s) X and Y axes feedrate (also used for delta Z axis)
  #define NOZZLE_PARK_Z_FEEDRATE 5      // (mm/s) Z axis feedrate (not used for delta printers)
#define PRINTJOB_TIMER_AUTOSTART
#define PRINTCOUNTER
#define LCD_LANGUAGE en
#define DISPLAY_CHARSET_HD44780 JAPANESE
#define LCD_INFO_SCREEN_STYLE 0
#define SDSUPPORT
#define REPRAP_DISCOUNT_FULL_GRAPHIC_SMART_CONTROLLER
#define SOFT_PWM_SCALE 0
#define SERVO_DELAY { 300 }

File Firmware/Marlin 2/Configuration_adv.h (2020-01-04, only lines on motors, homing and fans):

#define E0_AUTO_FAN_PIN FAN1_PIN
#define E1_AUTO_FAN_PIN -1
#define E2_AUTO_FAN_PIN -1
#define E3_AUTO_FAN_PIN -1
#define E4_AUTO_FAN_PIN -1
#define E5_AUTO_FAN_PIN -1
#define CHAMBER_AUTO_FAN_PIN -1
#define X_HOME_BUMP_MM 0
#define Y_HOME_BUMP_MM 0
#define Z_HOME_BUMP_MM 2
#define HOMING_BUMP_DIVISOR { 2, 2, 4 }  // Re-Bump Speed Divisor (Divides the Homing Feedrate)
#define MICROSTEP_MODES { 16, 16, 16, 16, 16, 16 } // [1,2,4,8,16]
#define DIGIPOT_I2C_MOTOR_CURRENTS { 1.0, 1.0, 1.0, 1.0, 1.0, 1.0, 1.0, 1.0 }  //  AZTEEG_X3_PRO
#define LIN_ADVANCE
  #define LIN_ADVANCE_K 0    // Unit: mm compression per 1mm/s extruder speed
#define ADVANCED_PAUSE_FEATURE
  #define ADVANCED_PAUSE_PURGE_FEEDRATE        3  // (mm/s) Extrude feedrate (after loading). Should be slower than load feedrate.
  #define ADVANCED_PAUSE_PURGE_LENGTH         50  // (mm) Length to extrude after loading.
  #define ADVANCED_PAUSE_RESUME_PRIME          0  // (mm) Extra distance to prime nozzle after returning from park.
    #define X_CURRENT       900        // (mA) RMS current. Multiply by 1.414 for peak current.
    #define X_CURRENT_HOME  X_CURRENT  // (mA) RMS current for sensorless homing
    #define X_MICROSTEPS     16    // 0..256
    #define Y_CURRENT       900
    #define Y_CURRENT_HOME  Y_CURRENT
    #define Y_MICROSTEPS     16
    #define Z_CURRENT       600
    #define Z_CURRENT_HOME  Z_CURRENT
    #define Z_MICROSTEPS     16
    #define E0_CURRENT      900
    #define E0_MICROSTEPS    16
  #define X_HYBRID_THRESHOLD     100  // [mm/s]
  #define X2_HYBRID_THRESHOLD    100
  #define Y_HYBRID_THRESHOLD     100
  #define Y2_HYBRID_THRESHOLD    100
  #define Z_HYBRID_THRESHOLD       3
  #define Z2_HYBRID_THRESHOLD      3
  #define Z3_HYBRID_THRESHOLD      3
  #define E0_HYBRID_THRESHOLD     30
  #define E1_HYBRID_THRESHOLD     30
  #define E2_HYBRID_THRESHOLD     30
  #define E3_HYBRID_THRESHOLD     30
  #define E4_HYBRID_THRESHOLD     30
  #define E5_HYBRID_THRESHOLD     30

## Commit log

2019-07-06 Create Bed Support C_1x.stl
    [Bed Support C_1x.stl]
2019-09-14 change log
    [3020 Cylinder.stl, 303010 Calibration Cube.stl, 4010 Fan Cover_3x.stl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]
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2019-09-15 name change
    [Panel Bottom Cut_1x.dxf, Panel Rear Cut_1x.dxf, Panel Side A Cut_1x.dxf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]
2019-09-15 update repo
    [Base Frame BOM RC1.0.xlsx, V-Baby BOM.xlsx]
2019-09-17 update order list
    [V-Baby BOM.xlsx]
2019-11-05 Update V-Baby BOM.xlsx
    [V-Baby BOM.xlsx]
2019-11-13 added drawings
    [BOM Base Frame Step 1.xlsx]
2019-11-17 step 2
    [BOM Base Frame Step 2.xlsx]
2019-12-30 upload spoolholder new
    [SpoolHolder 1x_SN_BO.stl, V-Baby BOM.xlsx]
2019-12-31 Create SpoolHolder B.f3d
    [SpoolHolder B.f3d]
2020-01-04 update4ing bom
    [Configuration.h, Configuration_adv.h, V-Baby BOM.xlsx]
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2020-01-05 30/1 gearing for Z
    [V-Baby BOM.xlsx]
2020-01-10 SHIM UPDATE
    [V-Baby BOM.xlsx]
2020-01-12 Bed support upgrade
    [Bed Support Buddy_2x_SB_BN.stl, Bed Support Middle_1x_SN_BN.stl, Fork Spacer_12x_SN_BO.stl]
2020-01-17 new files
    [Layer Fan Buddy A_1x_SN_BN.stl, Layer Fan Buddy B_1x_SN_BN.stl, Panel Bottom_Cut Pattern_1x.dxf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]
2020-03-21 Update Bed Lift Idler Buddy_2x_SN_BY.stl
    [Bed Lift Idler Buddy_2x_SN_BY.stl]
2020-03-21 updated belt anchor front bottom
    [Z Belt Bottom Anchor_1x_SN_BN.stl, Z Belt Front Bottom Anchor_1x_SN_BN.stl]
2020-03-21 Update Z Belt Buddy Front_1x_SB_BY.stl
    [Z Belt Buddy Front_1x_SB_BY.stl]
2020-03-21 Update Bed Support Middle_1x_SN_BN.stl
    [Bed Support Middle_1x_SN_BN.stl]
2020-03-22 moved face 1mm
    [Titan Extruder Rear Buddy_1x_SN_BN.stl, V6 Hotend Clamp_BL Touch_1x_SB_BN.stl]
2020-03-22 new usb cover
    [4010 Fan Cover_2x.stl, 4040 USB Cover.stl]
2020-03-23 skr 13 info
    [4040 USB Cover.stl]
2020-03-26 duet wifi added to list
    [V-Baby BOM.xlsx]
2020-03-27 update bom
    [Panel Bottom_Cut Pattern_1x.dxf, Panel Top-Front_Cut Pattern_1x.dxf, Panel Top-Rear_Cut Pattern_1x.dxf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]
2020-03-28 added bracket worm gear
    [Bed Support Middle_1x_SN_BN.stl, Wormgear Buddy B_1x_SN_BN.stl]
2020-03-28 Update Wormgear Buddy A_1x_SN_BN.stl
    [Wormgear Buddy A_1x_SN_BN.stl]
2020-03-29 Z update
    [Layer Fan Buddy A_1x_SN_BN.stl, Layer Fan Buddy B_1x_SN_BN.stl, Layer Fan Shroud_1x_SA_BN.stl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]
2020-03-31 adjustable legs
    [Adjustment_Leg_Base_4x_SN_BN.stl, Adjustment_Leg_Screw_4x_SN_BN.stl]
2020-04-01 Update Cable Loom Junction Lid_1x_SB_BN.stl
    [Cable Loom Junction Lid_1x_SB_BN.stl]
2020-04-02 new simpler cable loom buddy for X axis
    [Cable Loom Buddy_1x_Lid_Option_SN_BN.stl, Cable Loom Buddy_1x_SN_BN.stl, Cable Loom Junction Lid_1x_SB_BN.stl]
2020-04-12 Updated BOM
    [V-Baby BOM.xlsx, Z Template Tool long.stl, Z Template Tool short.stl]
2020-04-15 Bed frame hooks
    [Bed Frame Hooks_2x_SN_BN.stl, Bed Support Buddy_2x_SB_BN.stl, Bed Support Corner Buddy_2x_SB_BN.stl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]
2020-04-16 New bed frame hook + changed config
    [Bed Frame Hook A_2x_SN_BN.stl, Bed Frame Hook B_2x_SN_BN.stl, Bed Frame Hooks_2x_SN_BN.stl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]
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2020-04-16 Create Duet Wifi Standoff 1x_SN_BN.stl
    [Duet Wifi Standoff 1x_SN_BN.stl]
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2020-05-06 small update on bases
    [Duet Controller Base1x_SN_BN.stl, Duet Wifi Standoff 1x_SN_BN.stl, SSR Base.stl]
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2020-05-07 Update Corner Loom Buddy_1x_SN_BN.stl
    [Corner Loom Buddy_1x_SN_BN.stl]
2020-05-07 sorting by name in list
    [V-Baby BOM.xlsx]
2020-05-16 moved files to new folder
    [4010 Fan Cover_2x.stl, 4040 USB Cover.stl, Adjustment_Leg_Base_4x_SN_BN.stl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]
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2020-07-06 Create Bed Frame Hooks_4x_SN_BO.stl
    [Bed Frame Hooks_4x_SN_BO.stl]
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2020-10-23 Add Bearing Spool Holder
    [Spool Holder Base 1x_SN_BN_100%.stl]
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2020-10-31 Create 303020 Calibration Cube.stl
    [303020 Calibration Cube.stl]
2021-01-19 panel cut pattern 250
    [250 Bottom Plate_1x.stl, 250 Panel Bottom_Cut Pattern_1x.dxf, 250 Panel Front_Cut Pattern_1x.dxf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]
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2021-01-30 Z lift idler source files
    [Bed Lift Idler Buddy_2x.f3d, Idler Buddy Front_1x.f3d, Idler Top Rear Buddy_1x.f3d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]
2021-02-06 XY Idler Buddy Upgrade - Tensioner added
    [Cable Loom Buddy_1x_SN_BN.stl, Extruder Buddy_1x_SB_BN.stl, XY Idler Buddy A_1x_SB_BN.stl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]
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2021-02-16 Create _XY Tension Fork 18mm_2x_SN_BN.stl
    [_XY Tension Fork 18mm_2x_SN_BN.stl]
2021-02-21 cleaned up firmware files in rrf
    [Extruder Buddy_1x_SB_BN.stl]
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2021-03-02 Elongated front Z belt tension buddy so there are more travel for tension
    [10mm Z Belt Buddy Front Spacer_1x_SN_BY.stl, 10mm Z Belt Buddy Front Tension_1x_SN_BN.stl, 10mm Z Belt Buddy Front_1x_SB_BO.stl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]
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2021-04-01 changed from mks board to btt is better
    [V-Baby BOM.xlsx]
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2021-04-05 updated bed support parts
    [Bed Support Center_1x_SN_BN.stl, Bed Support Corner_2x_SN_BN.stl, Bed Support Corner_2x_SN_BN_100%.stl]
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2021-04-20 Added bolt for Z drive gear
    [V-Baby BOM.xlsx]
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2021-05-21 idler correction 10mm 20T
    [V-Baby BOM.xlsx]
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2021-09-12 bom update for 10mm belt
    [V-Baby BOM.xlsx]
2021-09-12 bom correction
    [V-Baby BOM.xlsx]
2021-11-02 updated belt length for the 300 size option. buy 4m not 2
    [V-Baby BOM.xlsx]

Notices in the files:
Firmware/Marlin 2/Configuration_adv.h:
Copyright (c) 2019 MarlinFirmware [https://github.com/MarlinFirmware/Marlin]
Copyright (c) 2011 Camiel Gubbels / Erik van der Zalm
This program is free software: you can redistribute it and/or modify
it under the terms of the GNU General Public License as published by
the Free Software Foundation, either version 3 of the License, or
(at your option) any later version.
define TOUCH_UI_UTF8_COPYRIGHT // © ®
